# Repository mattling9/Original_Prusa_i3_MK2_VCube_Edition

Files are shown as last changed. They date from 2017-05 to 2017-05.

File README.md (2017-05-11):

# Original Prusa i3 MK2 VCube Edition

Alternate Text for the Rendering of the VCube Edition.

[teaser]: http://imgur.com/bSvs2ah.jpg "VCube Rendering in CATIA"

https://www.thingiverse.com/thing:2267810

## *Disclaimer

**You Do This Modification At Your Own Risk**

I am not responsible for any damages / injuries that might arise from the usage of all material, including but not limited to ideas, documentation, diagrams, that you get from this github.  All precautions and safety protection should be taken and only attempt it if you are experienced in this area.

## What is the Original Prusa i3 MK2 VCube Edition?

The name "VCube" is based on two factors. The 'V' Represents that the majority of the frame uses 20mmx40mm Black Anodised "V-Slot" Aluminium Extrusions. The 'Cube' part of the name is because the frame resembles a cube. Simple.

### Key Features:

- Dramatically Increased Frame Strength
- Reduced Noise From the Printer
- Reduces Time and Effort to Calibrate the Printer.
- Can easily be Enclosed by Screwing on Any Sheet Material.
- Seperate Compartment to House Electronics, to Reduce Overheating.
- V-Slot Rails Provide Huge Customizability, Including Support For RPi-Camera, LED-Holders Ect..

The Original Prusa i3 MK2 VCube Edition uses as many parts as possible from the Original Prusa i3 MK2. A link to the Prusa Research© website can be found here: http://www.prusa3d.com/. I love the Original Prusa i3 MK2 and the high quality parts it uses, combined with cheap 3d printed parts to reduce the cost and make it affordable. Combine this with a lot of Research and Development from Prusa Research©, and you have a printer that can compete with £1000+ printers.

## Bill of Materials

Here are all of the materials i purchased for the build. I Purchased **ALL** of my parts together from [Ooznest](http://ooznest.co.uk/) in the UK. The company sold every part i needed at a very reasonable price all with Next Day Shipping. if you don't mind waiting 4-8 weeks shipping or you are outside the UK, i would suggest you can source your materials from places like [AliExpress](https://www.aliexpress.com/) or even [Ebay](http://www.ebay.com/).

### Essentials

These are the parts essential to the build. There is no replacement or alternatives. The Aluminium Extrusions can be any colour, i chose black to match my colour scheme. The M5 Bolts must be Low Profile in order to work with the Aluminium Cast Corners.

| Image 	| Reference | Part 	| Quantity 	| Notes 	|
|:---:	|:---:	|:---:	|:---:	|:---:	|
| V-Slot Photo 	| Corner Leg Extrusions 	| [2020 V-SLOT EXTRUSION 700MM](http://ooznest.co.uk/V-Slot/Linear-Rails/V-Slot-Linear-Rail-2020mm) 	| 4 	| <ul><li>Colour: Black</li><li>Length Range: 601-700mm</li><li>Precise Length: 700mm</li><li>M5 Tapping Service: Both Ends</li></ul> |
| V-Slot Photo 	| Side Extrusions 	| [2040 V-SLOT EXTRUSION 520MM](http://ooznest.co.uk/V-Slot/Linear-Rails/V-Slot-Linear-Rail-2040mm) 	| 6 	| <ul><li>Colour: Black</li><li>Length Range: 501-600mm</li><li>Precise Length: 520mm</li><li>M5 Tapping Service: None </li></ul>|
| V-Slot Photo 	| Front and Back Extrusions 	| [2040 V-SLOT EXTRUSION 400MM](http://ooznest.co.uk/V-Slot/Linear-Rails/V-Slot-Linear-Rail-2040mm) 	| 8 	| <ul><li>Colour: Black</li><li>Length Range: 301-400mm</li><li>Precise Length: 400mm</li><li>M5 Tapping Service: None </li></ul> |
| M5 Bolt Photo 	| 8mm M5 Bolt 	| [M5 LOW PROFILE 8MM](http://ooznest.co.uk/V-Slot/Bolts/Low-Profile-M5-Bolts) 	| 125 	| <ul><li>Bolt Length: 8mm</li><li>Pack Quantity: 5x 25</li></ul> |
| Tee Nut Photo 	| Tee Nuts 	| [M5 DROP IN TEE NUTS](http://ooznest.co.uk/Drop-In-Tee-Nuts) 	| 125 	| <ul><li>Thread Size: M5</li><li>PackQuantity: 5x 25</li></ul> |
| Cast Corner Photo 	| Cast Corner 	| [90 DEGREE CAST CORNER](http://ooznest.co.uk/V-Slot/Brackets/90-Degree-Cast-Corner) 	| 48 	| Can be replaced with printed ones. |

### Optional Parts

These parts are only optional and are not necessary to build the VCube Frame.

#### 3D Printed Cast Corners

| Image | Reference | Part | Quantity | Notes |
|:---:|:---:|:---:|:---:|:---:|
| Cast Corner Photo | Printed Cast Corner | ABS 90 DEGREE CAST CORNER | 16 | none  |

The Aluminium Cast Corners can be quite expensive, hterefore you can 3d print the Cast Corners. I have provided an .stl file for the cast corners in the Printed Parts folder. **BEWARE**, the printed ones are a lot weaker than the cast aluminium so i would advise not to use for printed ones for every corner. I use cast ones for the main construction of the frame and printed ones to hold the 2x 400mm Extrusions to mount the Y Axis on.

#### GT2 1 Meter Belt

| Image | Reference | Part | Quantity | Notes |
|:---:|:---:|:---:|---:|:---:|
| GT2 Belt Photo | GT2 Belt | [GT2 OPEN TIMGING BELT 1M](http://ooznest.co.uk/GT2-Timing-Belt) | 1 | Length: 1 Meter  |

The VCube design requires the X Motor to be moved about 40mm the the right. This means that the belt will have to be 40mm shorter than the original one. I did not want to cut my Original Pursa i3 MK2 belt, incase i wanted to put the printer back in the Original frame, so i purchased a new one. 1 Meter is the perfect length for the belt.

#### 10mm M5 Low Profile Bolts
| Image | Reference | Part | Quantity | Notes |
|:---:|:---:|:---:|:---:|:---:|
| 10mm M5 Bolt Photo | 10mm M5 Bolt | [10MM M5 LOW PROFILE BOLT](http://ooznest.co.uk/V-Slot/Bolts/Low-Profile-M5-Bolts) | As Many As You Want | Bolt Length: 10mm  |

In order to add additional printed parts to the frame, i am using 10mm M5 Low profile bolts. I chose 10mm over the original 8mm as it allowed me to have thicker, stronger printer parts to connect to the frame. An example of an 'Additional Part' is something like a camera mount for the PPi-Camera connected to Octoprint. **Remember to purchase more Tee-Nuts for the 10mm M5 nuts.**

#### NEMA17 Stepper Motor Dampener
| Image | Reference | Part | Quantity | Notes |
|:---:|:---:|:---:|:---:|:---:|
| NEMA17 Dampener Photo | NEMA17 Dampener | [NEMA17 STEPPER MOTOR DAMPER](http://ooznest.co.uk/Stepper-Motor-Damper) | 2 or 4| Size: NEMA17  |

NEMA17 Stepper Motor Dampeners, reduce the vibration transmitted from the stepper motors into the frame. They have provided a huge difference in noise when connected to all of the axis. I have suggested '2 or 4' in the Quantity, because they are only really needed on the X and Y Axis which requires 2. You can put 2 on the Z axis but it will not make any difference during a normal print.

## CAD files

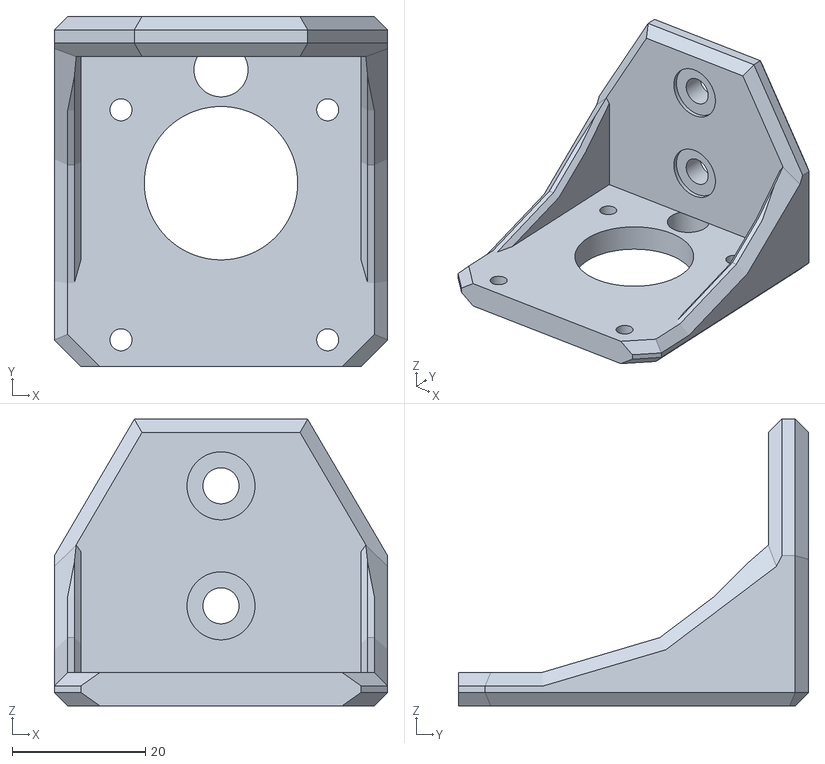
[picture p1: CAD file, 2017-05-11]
Printed Parts/Motor Mount.stl
50.0 x 52.5 x 43.0

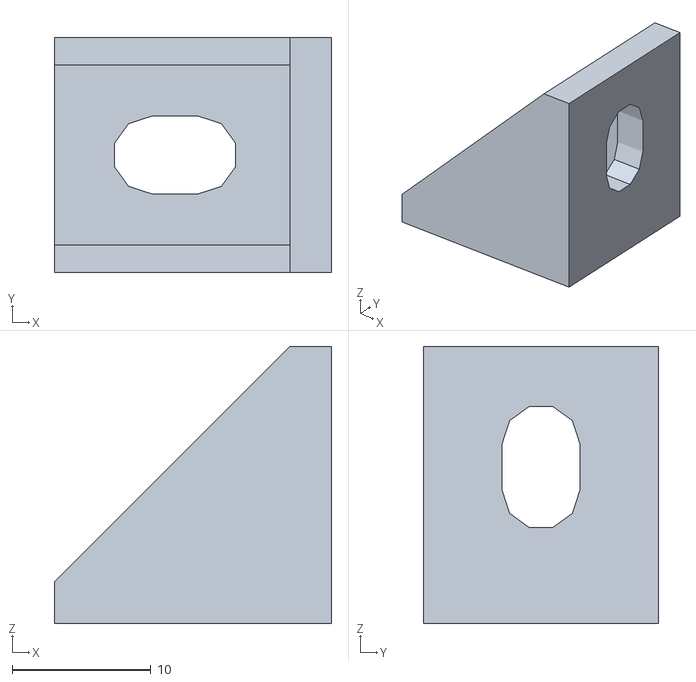
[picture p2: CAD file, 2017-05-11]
Printed Parts/3D Printed Cast Corner.stl
20.0 x 17.0 x 20.0

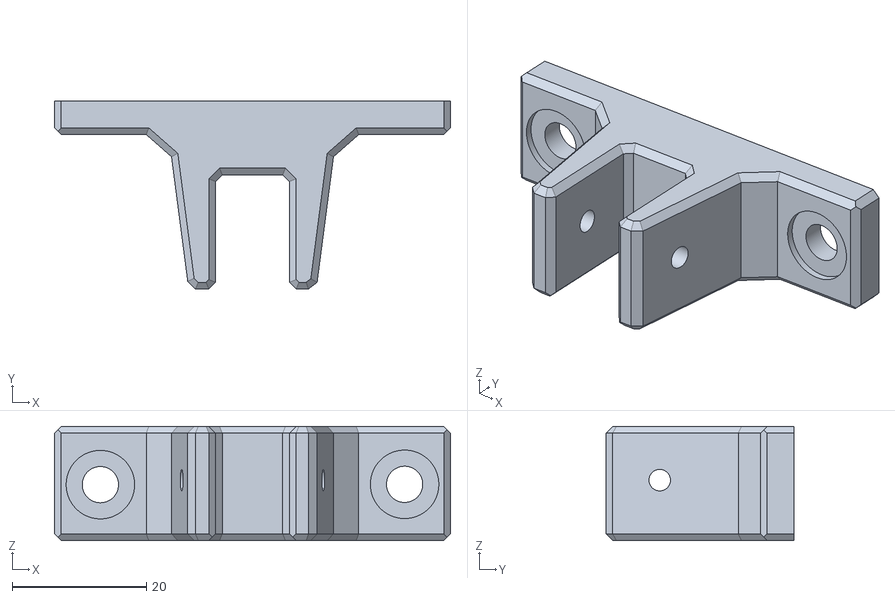
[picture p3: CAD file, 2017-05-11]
Printed Parts/Y-Belt Holder.stl
59.0 x 28.0 x 17.0

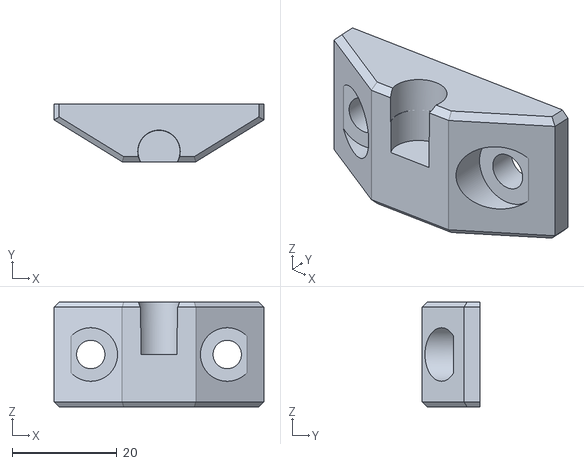
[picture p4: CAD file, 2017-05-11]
Printed Parts/Y Rod Holder.stl
40.0 x 11.0 x 20.0

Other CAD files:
CATIA Models/3D Printed Cast Corner.CATPart
CATIA Models/Y Rod Holder.CATPart
CATIA Models/Y-Belt Holder.CATPart

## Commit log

2017-05-11 Y-Rod Holder
    The Y-Rod Holders, for the use with M5 10mm Low Profile Nuts with 2x Neoprene Washers for noise dampening
    [Y Rod Holder V4.stl]
2017-05-11 Rename Y Rod Holder V4.stl to Printed Parts/Y Rod Holder V4.stl
    [Y Rod Holder V4.stl]
2017-05-11 Rename Y Rod Holder V4.stl to Y Rod Holder.stl
    [Y Rod Holder.stl]
